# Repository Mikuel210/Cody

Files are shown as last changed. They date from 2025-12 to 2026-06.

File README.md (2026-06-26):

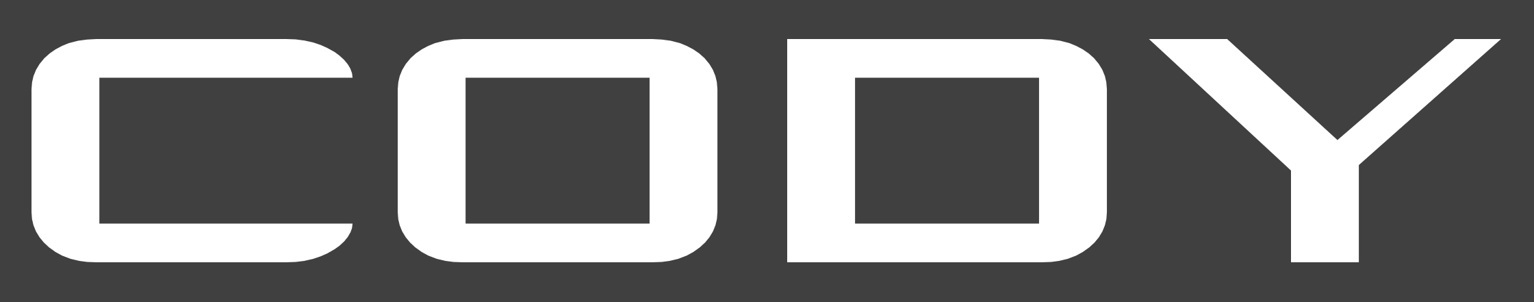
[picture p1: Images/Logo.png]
Cody


**Cody is a robot for the next season of WRO Robomission Senior.** 

The World Robot Olympiad (WRO) is a global robotics competition. For the Robomission challenge, you have to design, build and program a robot to complete a set of challenges on a board in under 2 minutes. Cody is our attempt at making our best robot so far, and I'm designing it to be faster, more precise and more reliable than all of our previous.

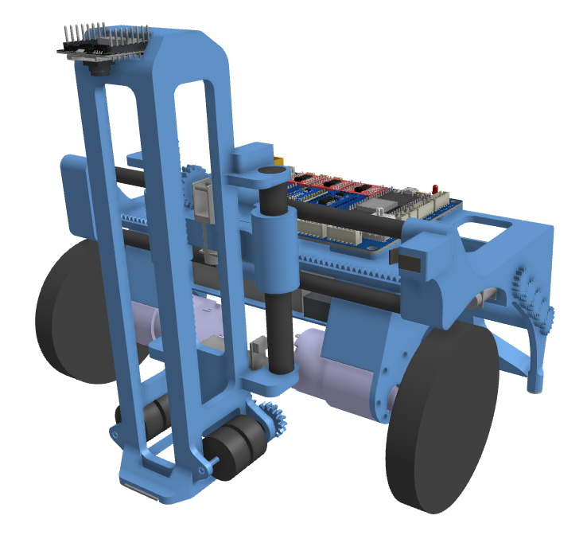
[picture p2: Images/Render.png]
Render


## This year's challenges

1. There is a mosaic with a randomized pattern of colors at the center of the board. You have to place a block of the right color in each square of the grid to score.

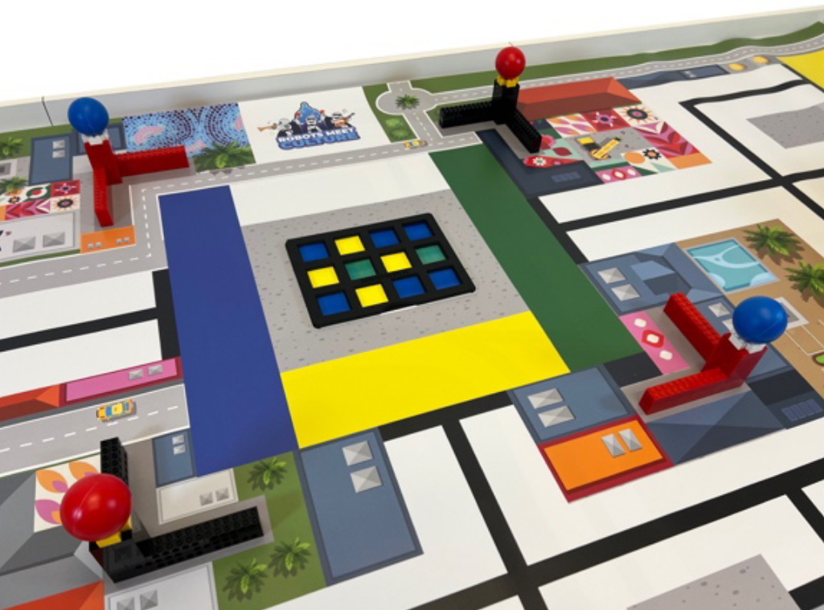
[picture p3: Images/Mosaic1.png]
Mosaic


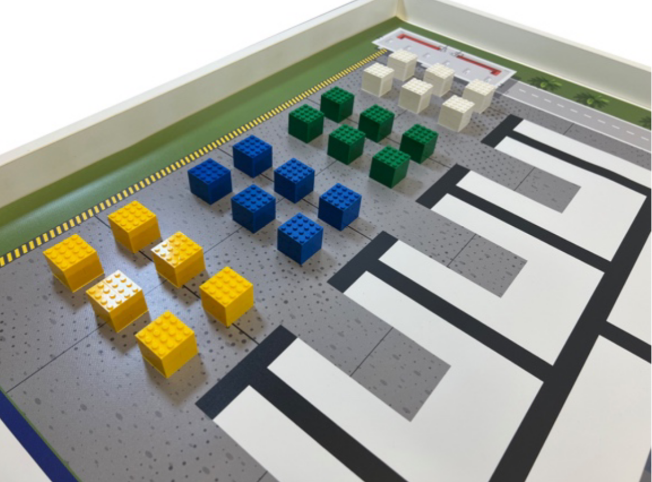
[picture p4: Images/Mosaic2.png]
Blocks


2. There are blocks of "cement" of different colors on the board. You have to carry the blocks of each color to their corresponding area.

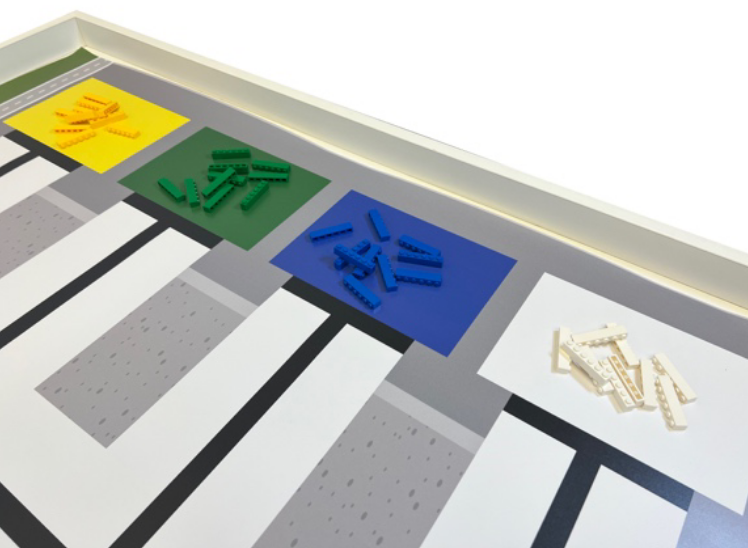
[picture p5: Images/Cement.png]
Cement


## Our solution

1. A toolhead grabs and drops blocks for the mosaic by using wheels

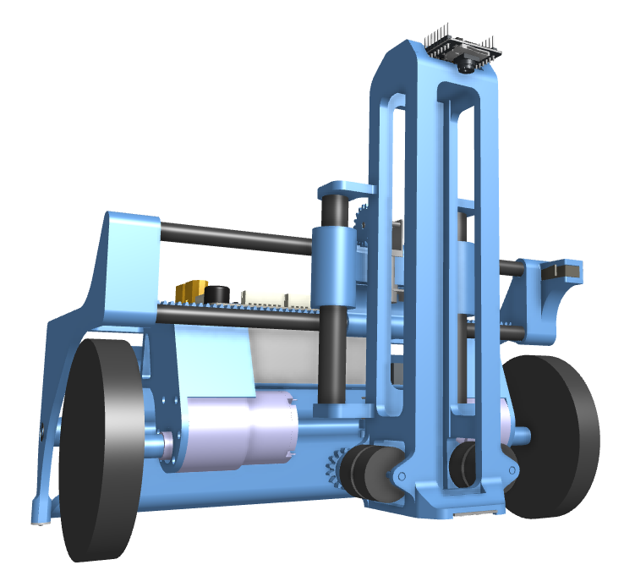
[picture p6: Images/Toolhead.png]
Toolhead


2. A mill picks up, carries and releases two colors of cement at a time

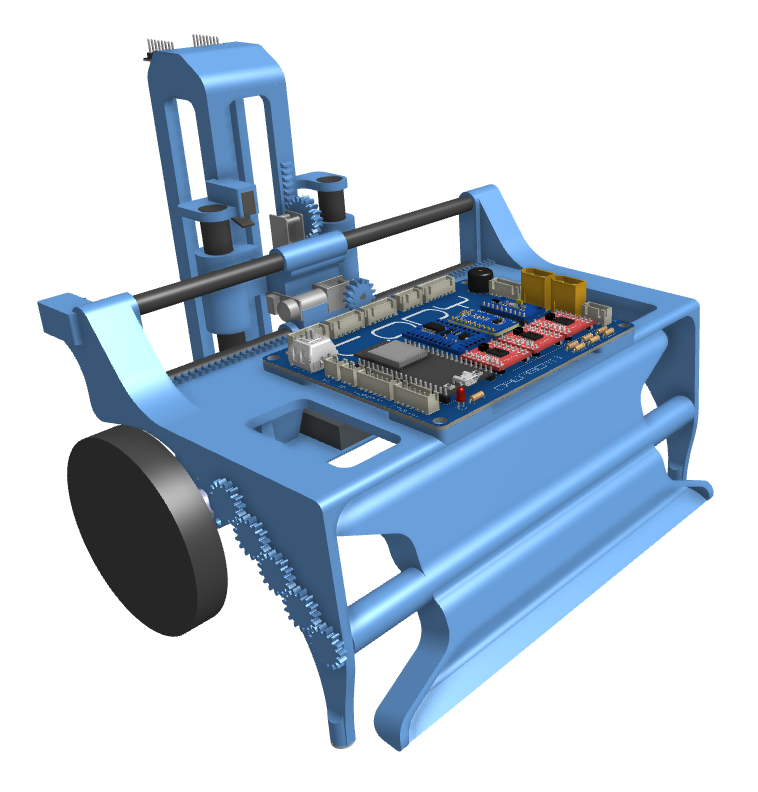
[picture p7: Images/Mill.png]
Mill


## How it works

- **Electronics:** I'm using an ESP32 as the microcontroller, an MPU9250 IMU for orientation and a TCS34725 color sensor for detecting the lines on the board. I'm also using an ADS1115 ADC for measuring the voltage of the battery and a PCF8575 GPIO expander.
- **Camera:** I'm using an ESP32-CAM to detect the color pattern of the mosaic.
- **Actuators:** I'm using JGB37-3530 motors for the wheels and N20 motors for the toolhead and for the mill. I'm using TB6612FNG drivers to control them.
- **Power:** I'm using a 3S 2200mAh LiPo battery for powering the robot. I'm also using a voltage regulator for powering the ESP32.
- **Structure:** I'm using 3D printed structural parts that have attachments for the components. I will be printing them out of PETG. I'm also using standard hardware such as bearings, carbon fiber rods and castor wheels.
- **Software:** I'm using odometry and a Pure Pursuit algorithm for control.

## Why I made this

My team has been using Lego Spike since we started competing, but it's starting to show its limitations. Last year, we went to the international final for the first time. Robomission had opened up to all hardwares for the first time this year, which means other teams could make faster, more precise and more reliable robots than what we could possibly do with Lego. I'm designing this robot to be faster, more precise and more reliable than our previous robots with the power of open hardware.

## PCB

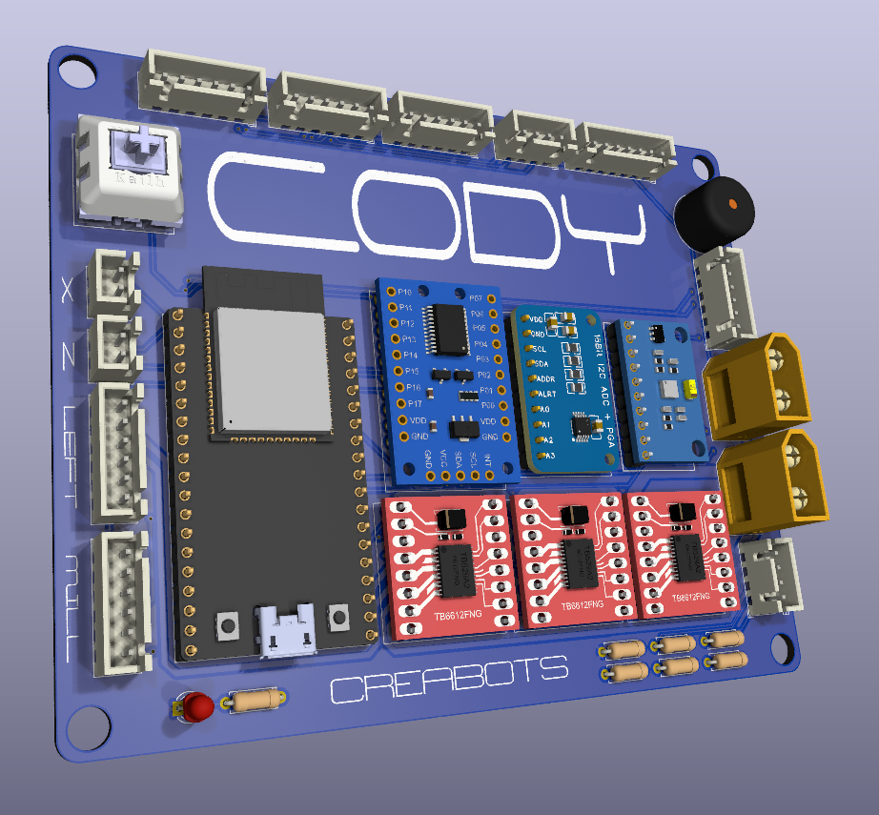
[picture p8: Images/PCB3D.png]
PCB 3D model


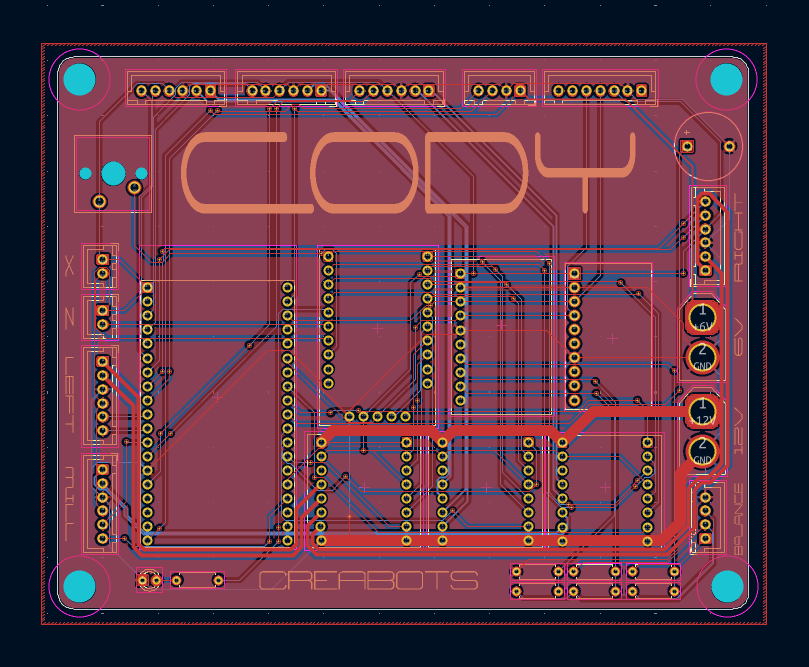
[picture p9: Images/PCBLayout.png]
PCB Layout


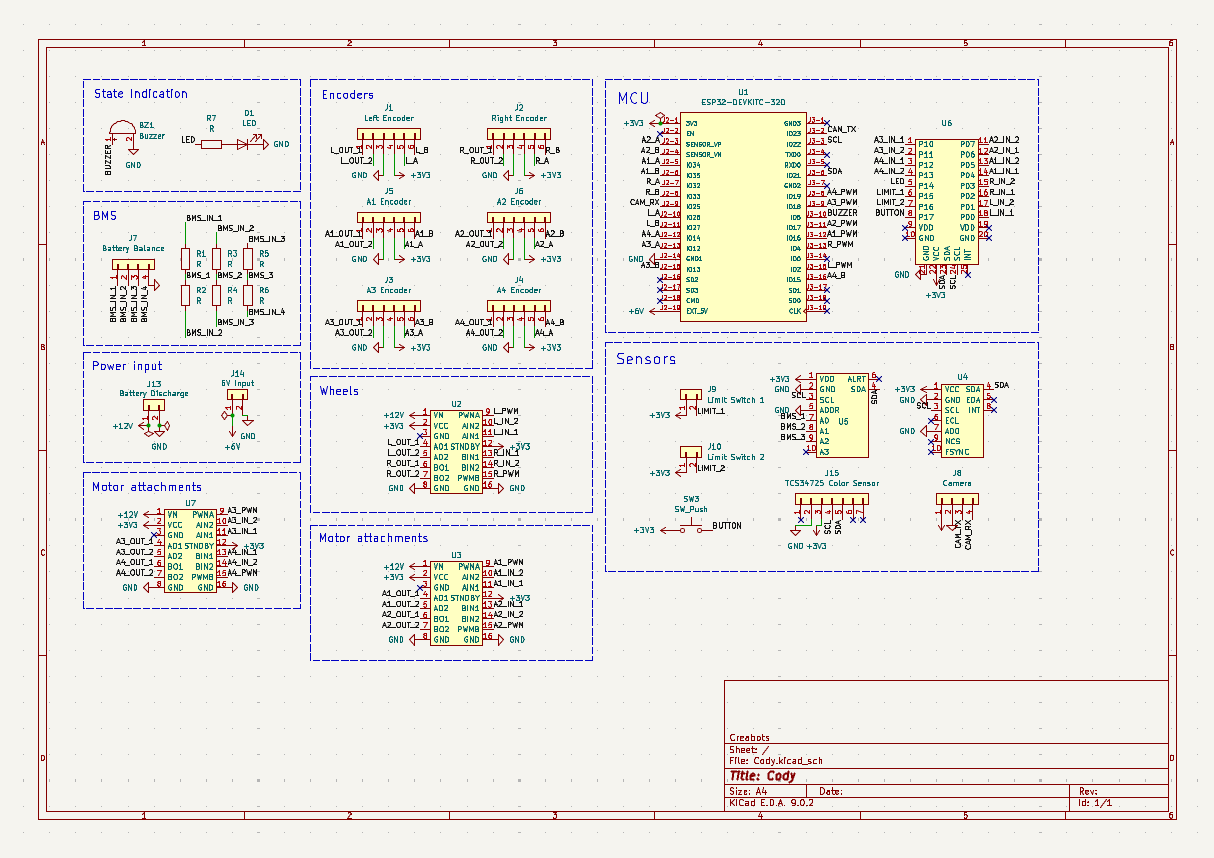
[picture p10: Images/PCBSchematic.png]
PCB Schematic


## Wiring diagram

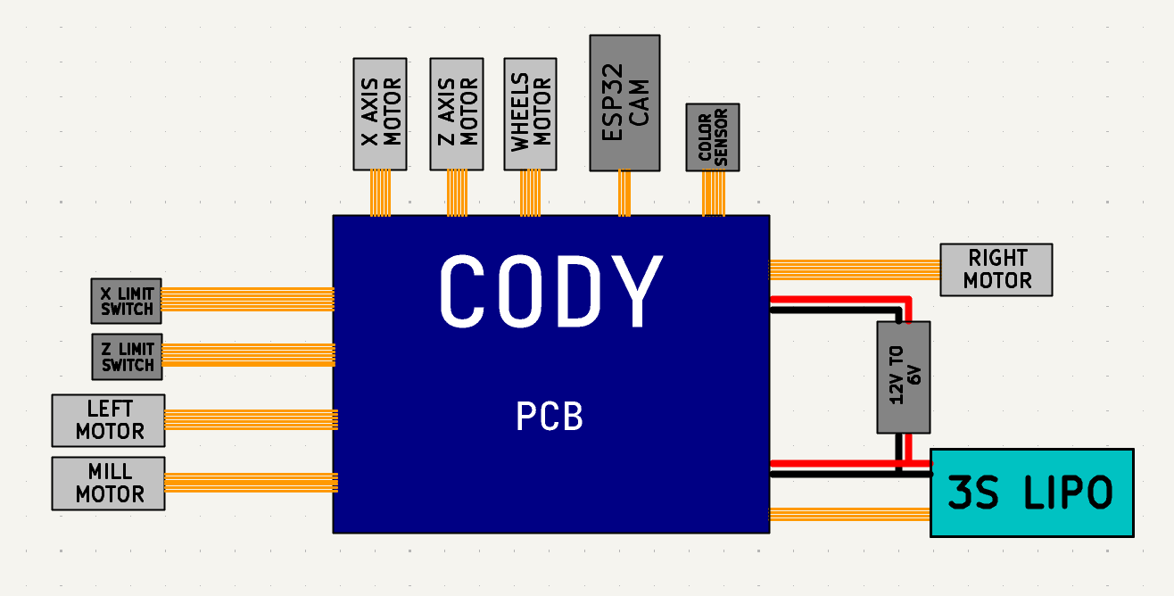
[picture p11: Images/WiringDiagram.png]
Wiring diagram


## Onshape Document

https://cad.onshape.com/documents/a1e1109ed4daddff079aebb8/w/75daa850bdae83d3a805f11b/e/0ab81b698f3d6ebcf8c57589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

## Cart screenshots

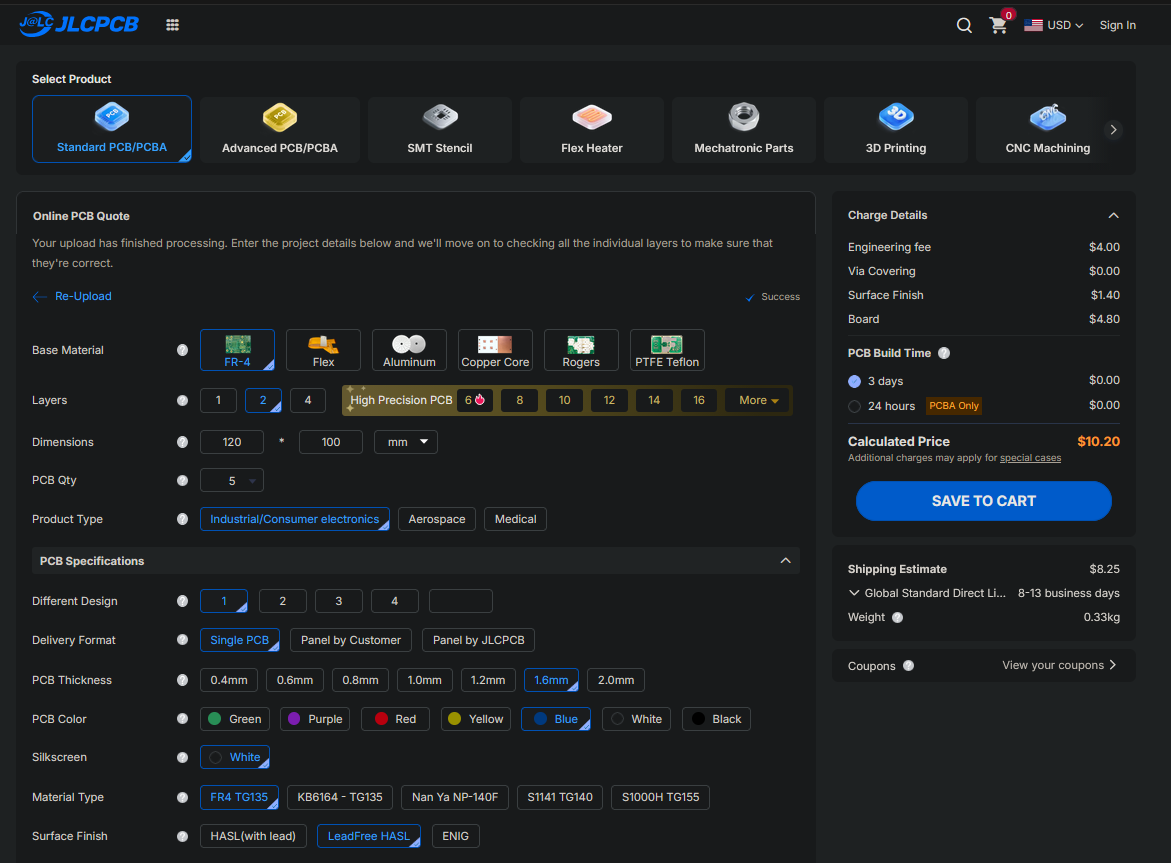
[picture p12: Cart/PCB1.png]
Cart screenshot

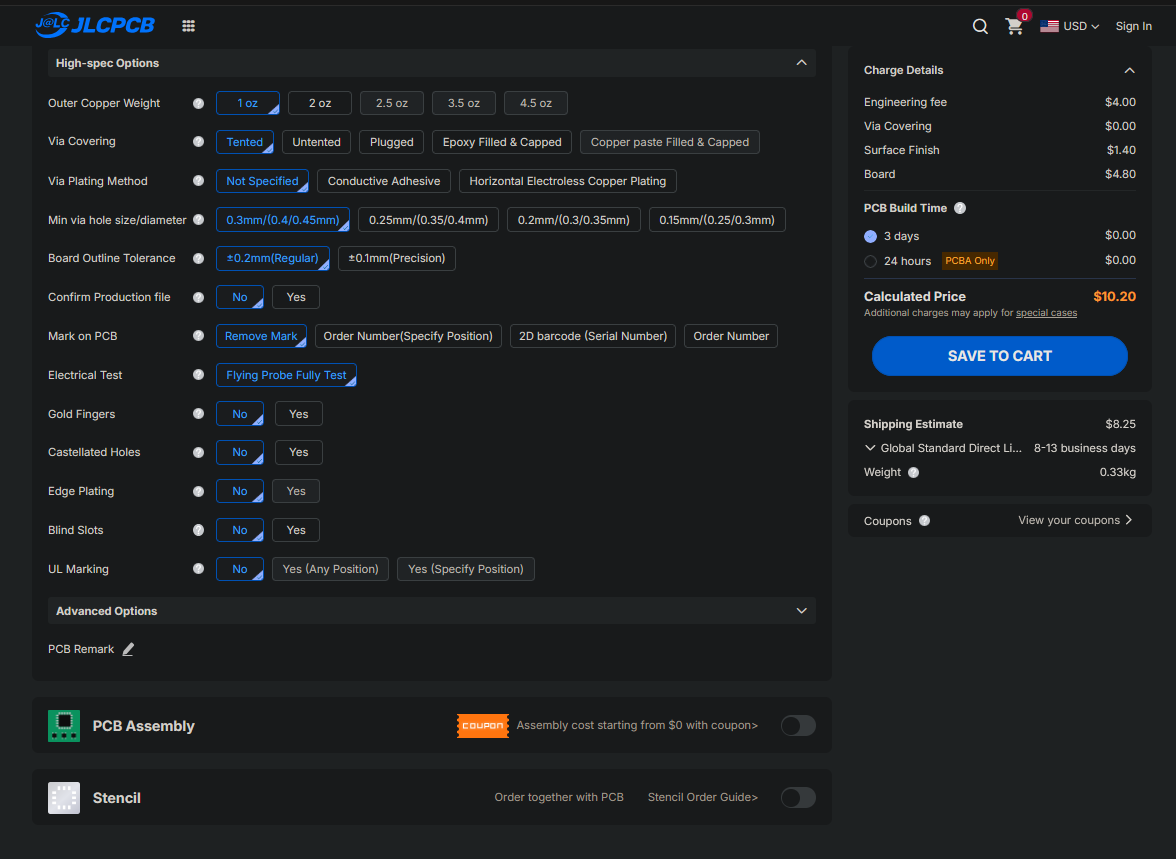
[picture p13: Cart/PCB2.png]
Cart screenshot

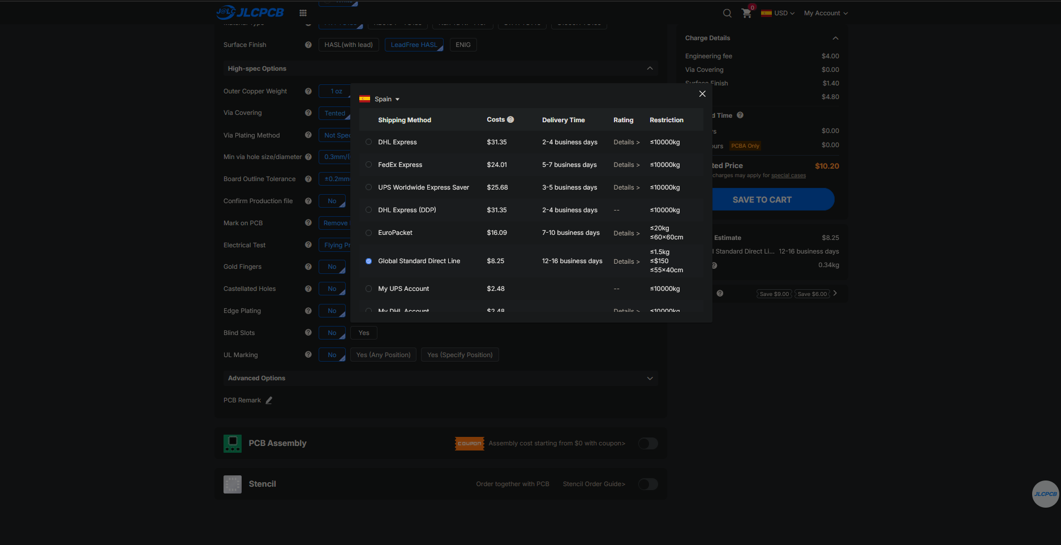
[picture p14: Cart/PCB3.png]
Cart screenshot

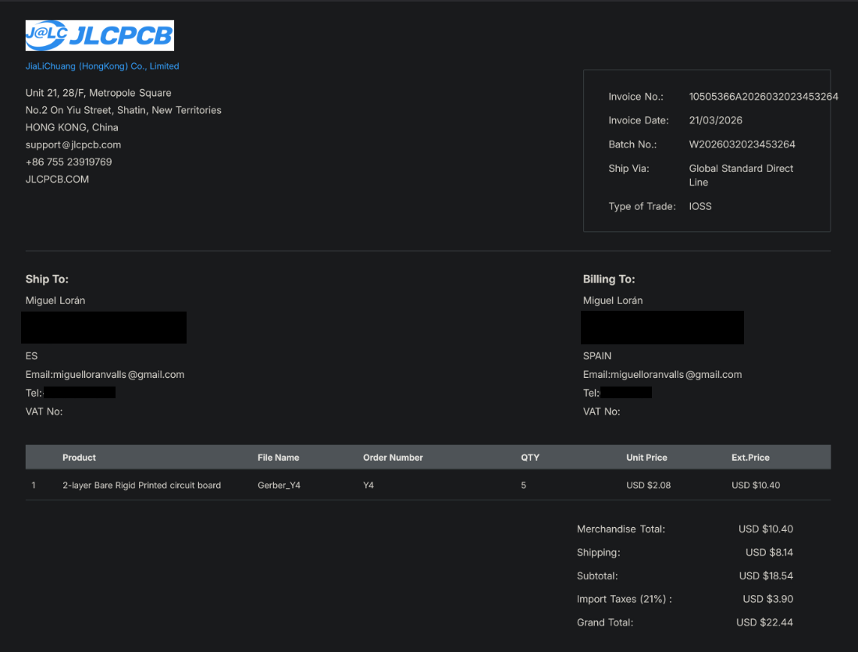
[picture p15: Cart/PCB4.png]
Cart screenshot

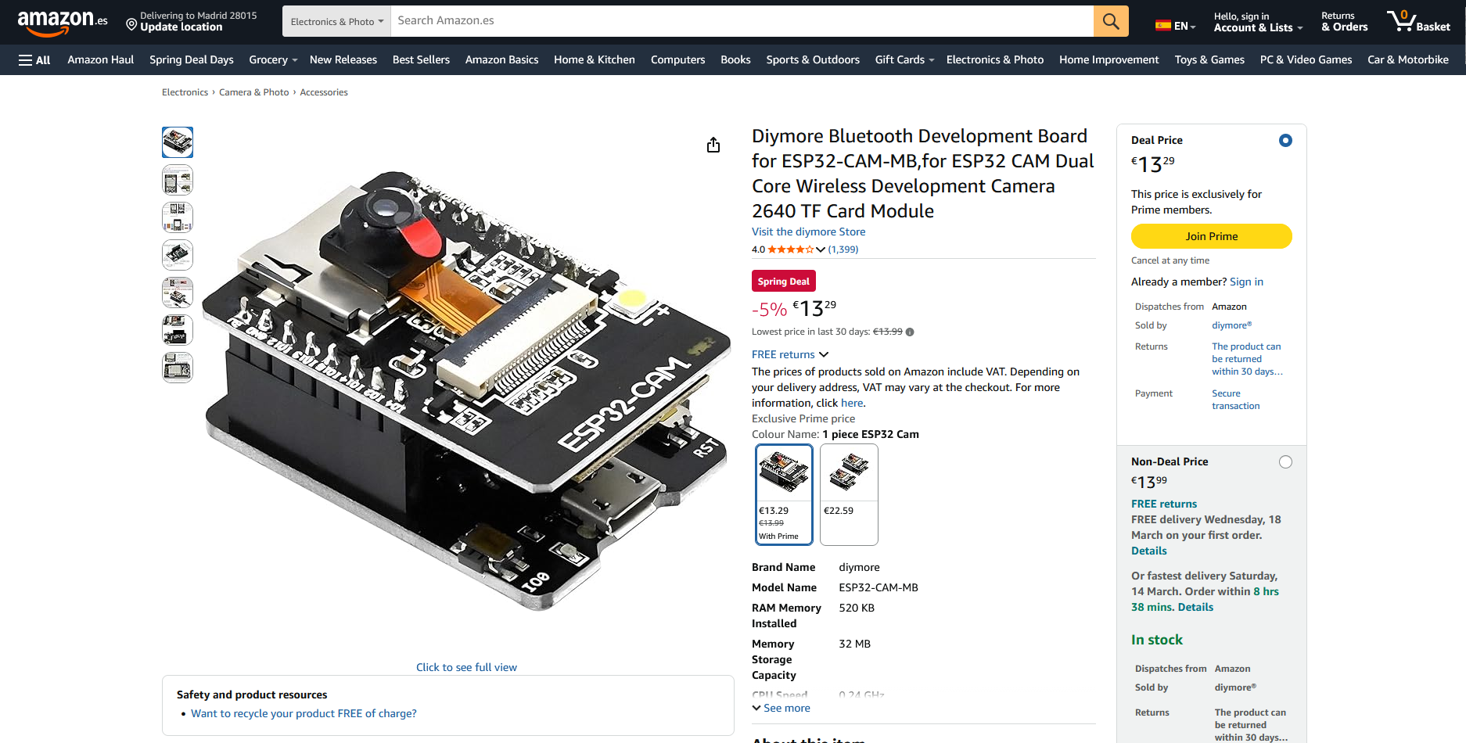
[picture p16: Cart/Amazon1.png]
Cart screenshot

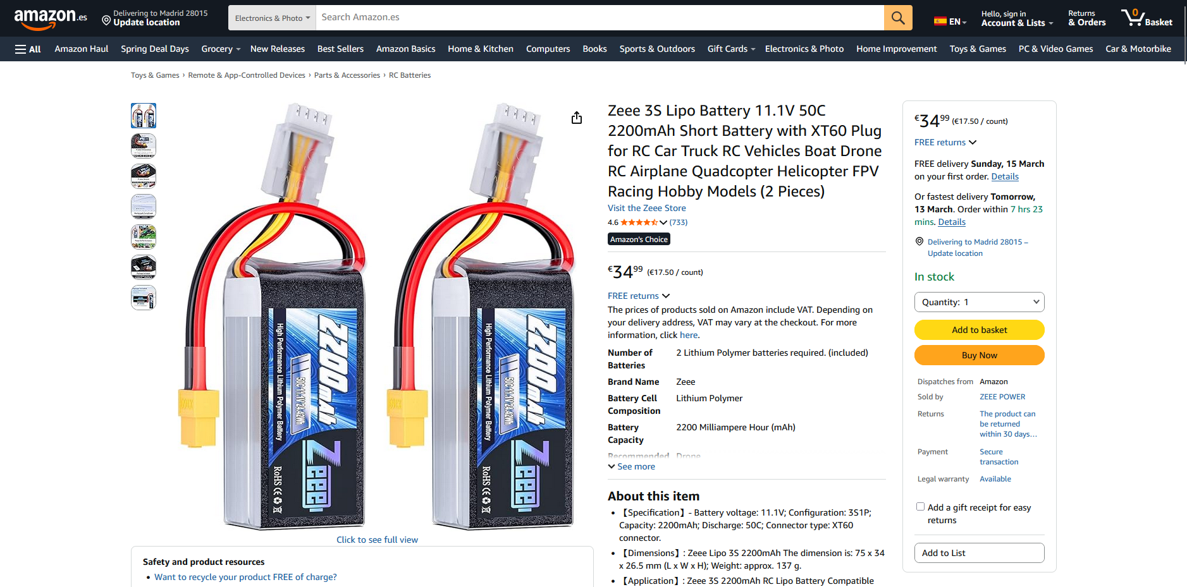
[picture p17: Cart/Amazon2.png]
Cart screenshot

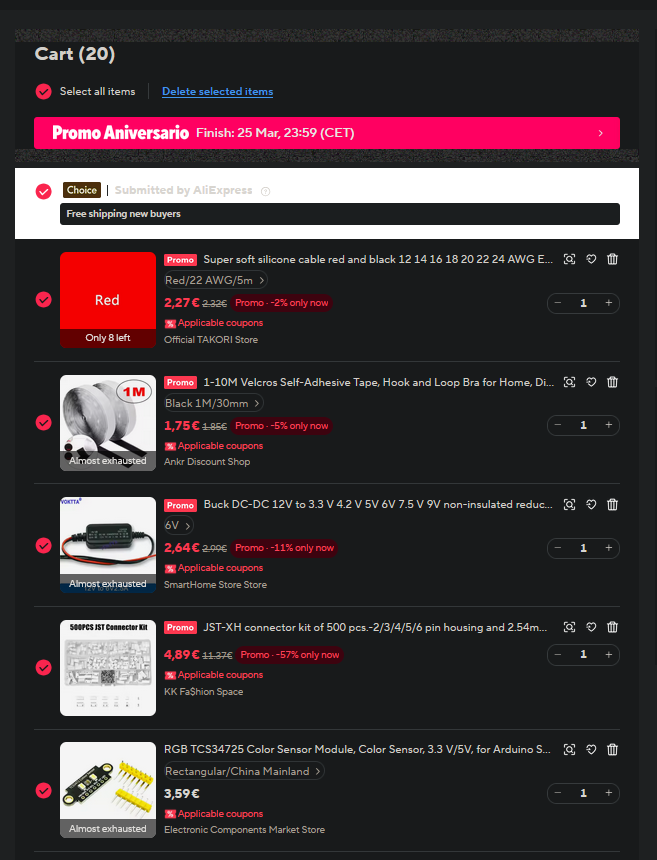
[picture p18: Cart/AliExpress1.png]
Cart screenshot

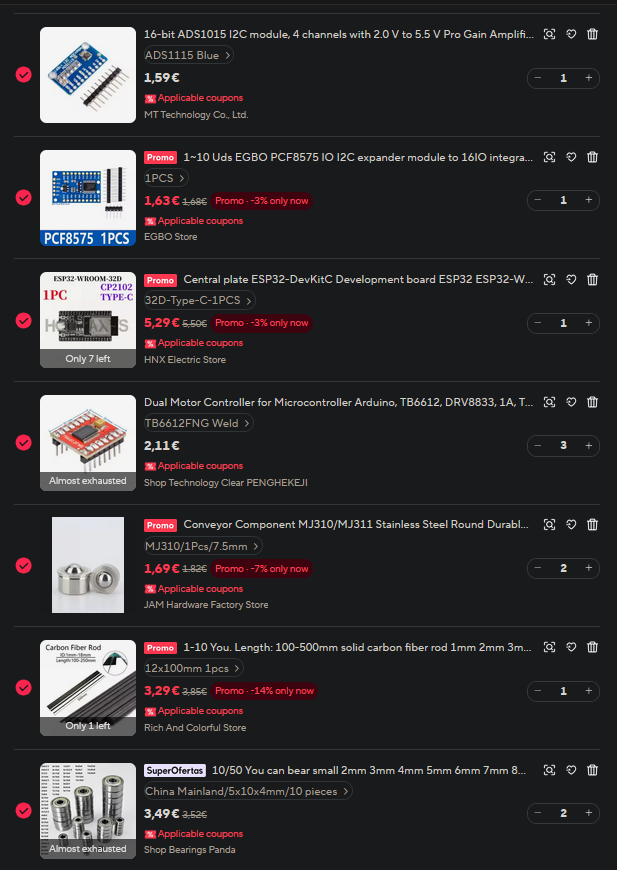
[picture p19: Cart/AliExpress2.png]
Cart screenshot


> Note: I will be buying two of the carbon fiber rods above but AliExpress didn't feel like allowing me to add more than one to my cart at the moment

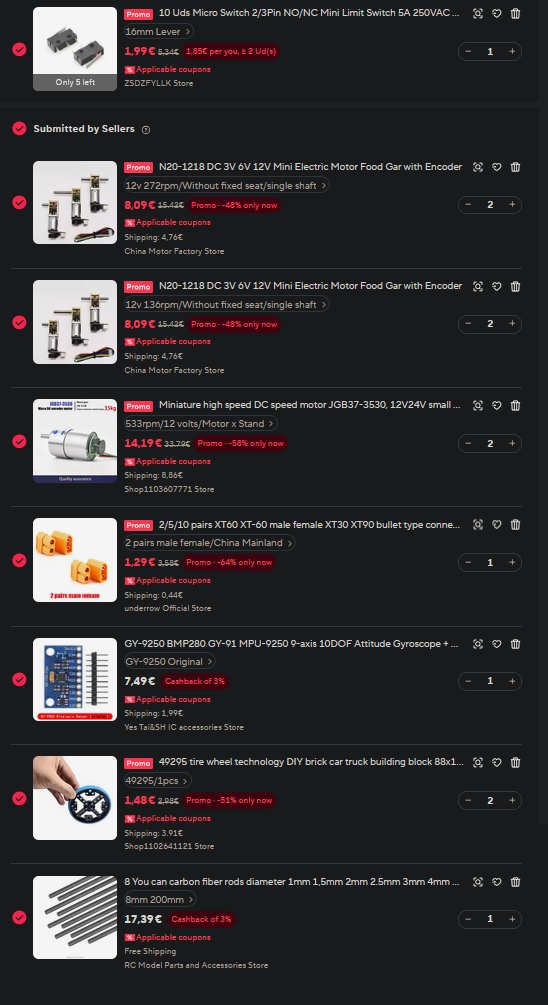
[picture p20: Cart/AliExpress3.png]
Cart screenshot

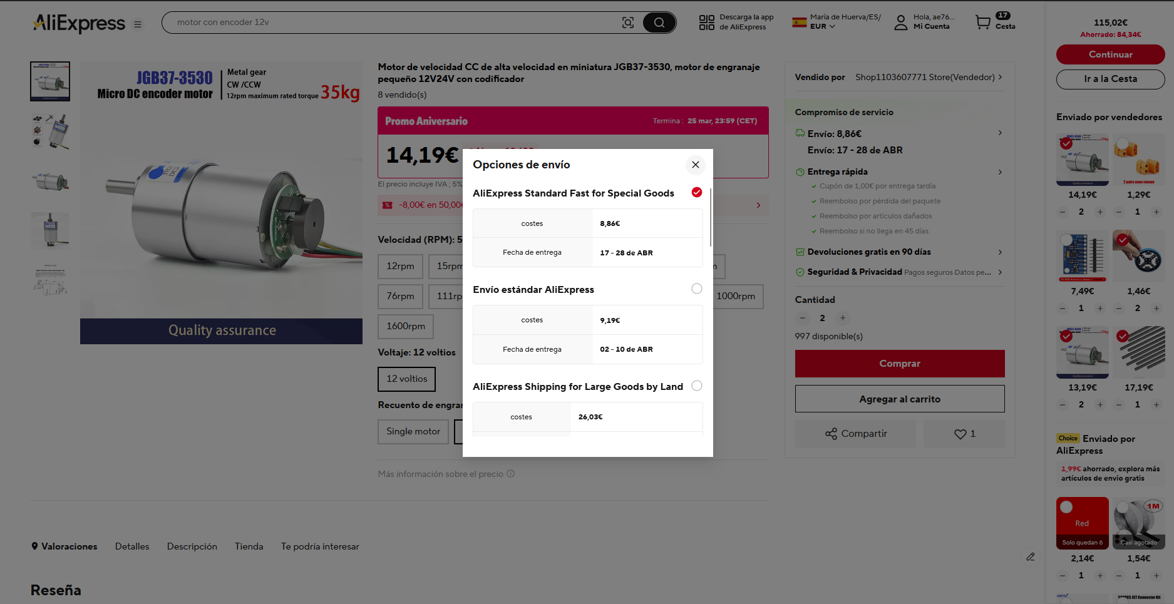
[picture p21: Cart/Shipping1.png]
Cart screenshot

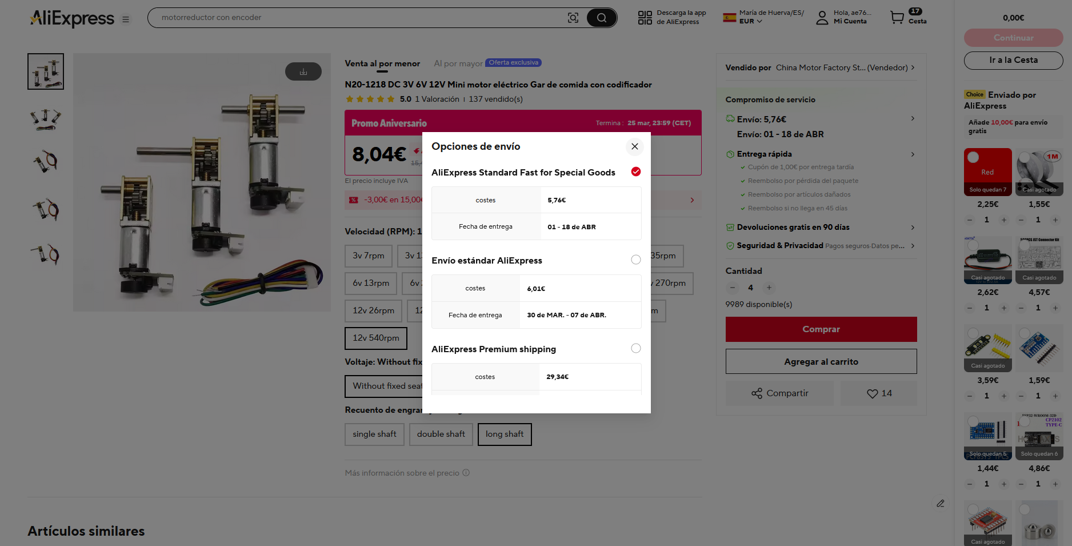
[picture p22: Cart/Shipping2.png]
Cart screenshot

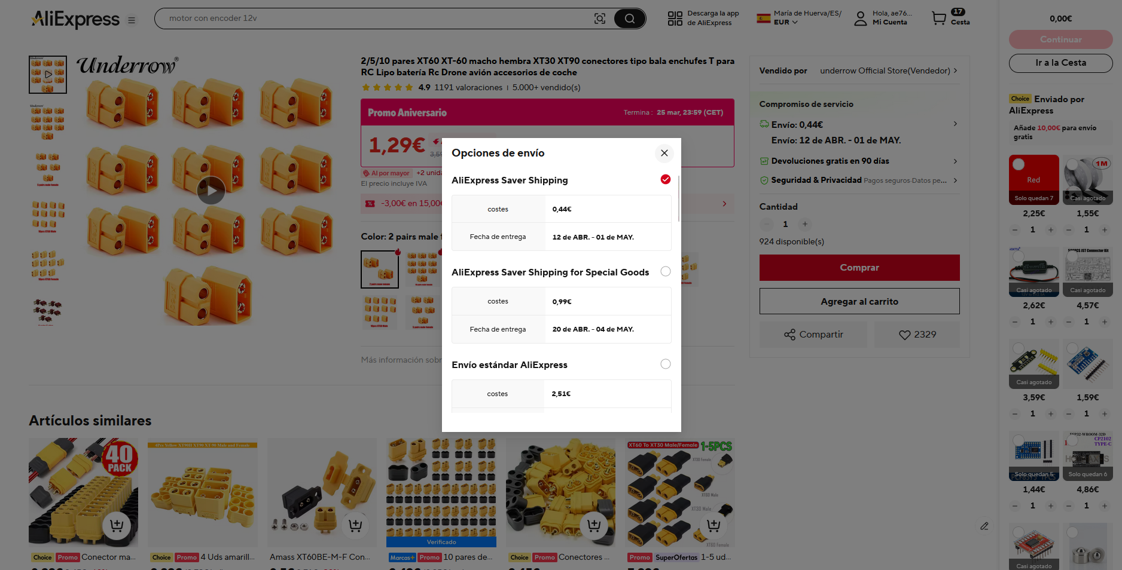
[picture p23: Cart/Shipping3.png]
Cart screenshot

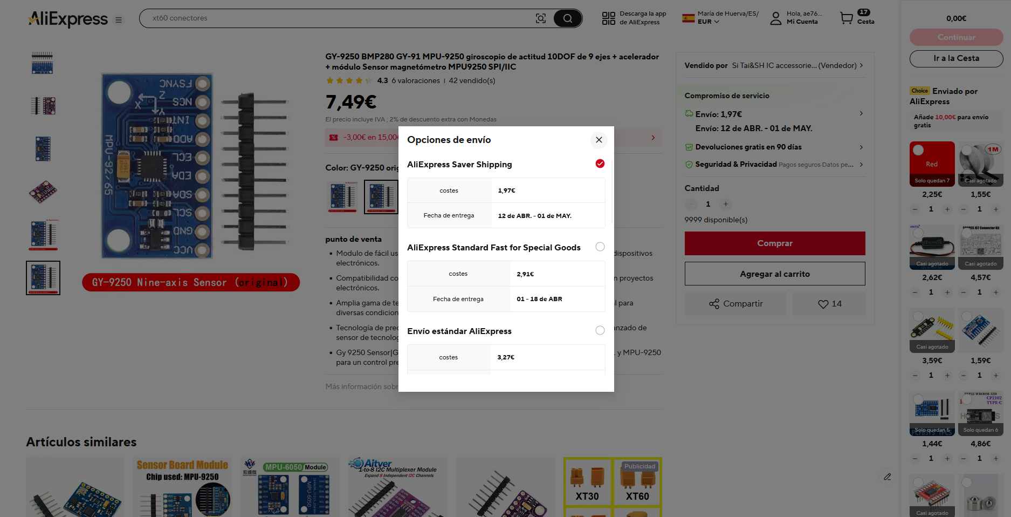
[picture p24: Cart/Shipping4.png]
Cart screenshot

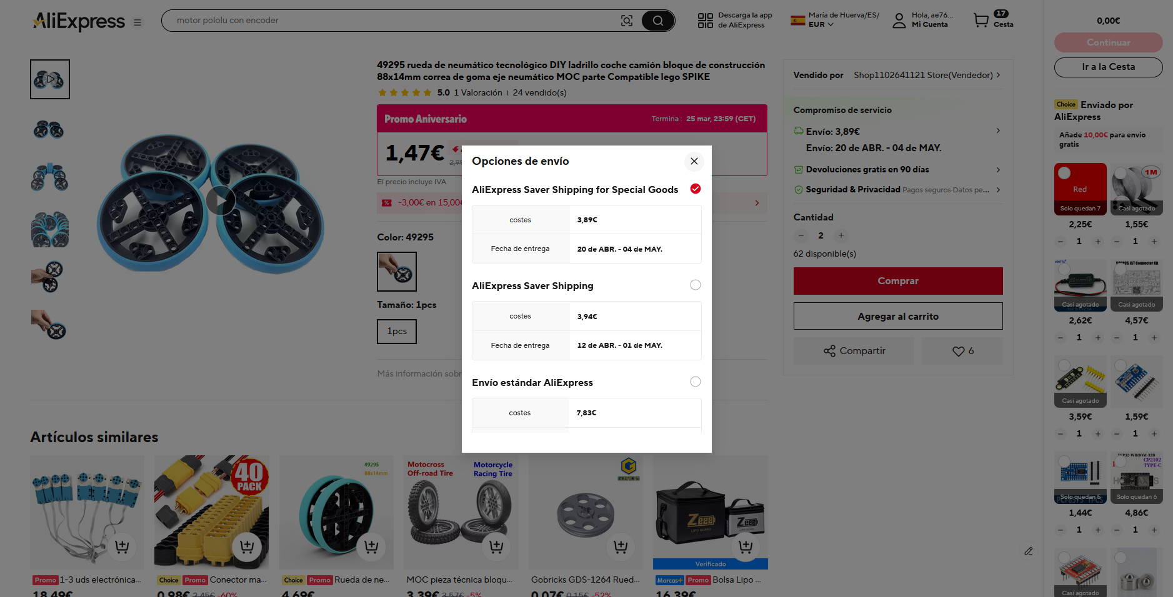
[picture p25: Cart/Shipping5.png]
Cart screenshot


## BOM

> Note that the amount to buy might be higher than the amount to be used because the item is sold in bulk

|Item |Amount|Amount to buy|Unit price|Total price |Link |Config |
|---|---|---|---|---|---|---|
|PETG |1 |0 |0,00 € |0,00 € |- |- |
|PCB |1 |1 |19,36 € |19,36 € |https://jlcpcb.com |- |
|Battery |2 |2 |17,50 € |34,99 € |https://www.amazon.es/Zeee-Bater%C3%ADa-Veh%C3%ADculos-Cuadric%C3%B3ptero-Helic%C3%B3ptero/dp/B0BYNSH6Q7|- |
|X Axis rods |2 |8 |2,17 € |17,39 € |https://es.aliexpress.com/item/4001063505625.html |8mm 200mm |
|Z Axis rods |2 |2 |3,29 € |6,58 € |https://es.aliexpress.com/item/1005006793821681.html |12x100mm 1pcs |
|Wheel motors |2 |2 |18,62 € |37,24 € |https://es.aliexpress.com/item/1005008730235398.html |533rpm 12V Motor x Stand |
|N20 motors |4 |4 |10,47 € |41,88 € |https://es.aliexpress.com/item/1005009284080839.html |136x2, 272x2 without fixed seat|
|Front wheels |2 |2 |3,44 € |6,87 € |https://es.aliexpress.com/item/1005010058308140.html |49295 1pcs |
|Back wheels |2 |2 |1,69 € |3,38 € |https://es.aliexpress.com/item/1005005334424631.html |7.5mm 1Pcs MJ310 |
|5x10x4 Bearing |11 |20 |0,35 € |6,98 € |https://es.aliexpress.com/item/1005007668446060.html |5x10x4mm |
|Buzzer |1 |0 |0,00 € |0,00 € |- |- |
|RGB LED |1 |0 |0,00 € |0,00 € |- |- |
|Resistors |7 |0 |0,00 € |0,00 € |- |- |
|Mechanical switch |1 |0 |0,00 € |0,00 € |- |- |
|Limit switches |2 |10 |0,20 € |1,99 € |https://es.aliexpress.com/item/1005008823539259.html |16mm Lever |
|TB6612FNG Motor drivers |3 |3 |2,11 € |6,33 € |https://es.aliexpress.com/item/1005006983040834.html |TB6612FNG Weld |
|ESP32 DevKitC |1 |1 |5,29 € |5,29 € |https://es.aliexpress.com/item/1005008256121637.html |32D-Type-C-1PCS |
|PCF8575 GPIO Expander |1 |1 |1,63 € |1,63 € |https://es.aliexpress.com/item/1005002073772322.html |1PCS |
|ADS1115 ADC |1 |1 |1,59 € |1,59 € |https://es.aliexpress.com/item/32311656694.html |ADS1115 Blue |
|MPU9250 IMU |1 |1 |9,48 € |9,48 € |https://es.aliexpress.com/item/1005009033822037.html |GY-9250 original |
|TCS34725 Color sensor |1 |1 |3,59 € |3,59 € |https://es.aliexpress.com/item/1005006292597348.html |Rectangular |
|XT60 Connectors |2 |2 |0,87 € |1,73 € |https://es.aliexpress.com/item/1005004628891959.html |2 pairs male female |
|JST-XH Connectors |9 |9 |0,54 € |4,89 € |https://es.aliexpress.com/item/1005008638438956.html |- |
|12V to 6V converter |1 |1 |2,64 € |2,64 € |https://es.aliexpress.com/item/1005007763337343.html |6V |
|ESP32-CAM |1 |1 |13,29 € |13,29 € |https://www.amazon.es/diymore-desarrollo-ESP32-CAM-MB-Bluetooth-inal%C3%A1mbrica/dp/B08X3GRK22 |- |
|Velcro for battery and converter|1 |1 |1,75 € |1,75 € |https://es.aliexpress.com/item/1005008938790125.html |Black 1M 30mm |
|Cable for sensors and motors |1 |1 |2,27 € |2,27 € |https://es.aliexpress.com/item/1005006566120439.html |5m 22 AWG |
|Cable for battery |1 |0 |0,00 € |0,00 € |- |- |
|TOTAL | | | |231,14 € ($267,79)| | |

---

Made with ❤️ for Blueprint thanks to Hack Club

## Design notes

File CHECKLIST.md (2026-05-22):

- [x] Finish BOM
- [x] Finish firmware
- [-] New renders
- [x] Update GitHub
- [x] Submit to Blueprint
- [x] Buy parts
- [x] Update CAD model
	- [x] New motors (N20 / N30)
	- [x] Limit switches
	- [x] Camera and color sensor
	- [x] Switch to CF rods
- [x] Check amperages and weight
- [x] Update PCB (01-04-2026)
	- [x] Add button
	- [x] Limit switch connectors
	- [x] Camera connector requires power pins
	- [x] Connector placement collides with X axis
	- [x] Make sure amperages work out
	- [x] Check I2C addresses
	- [x] Better routing
	- [x] Proper silkscreen for connectors
- [x] Update Blueprint journal and repo
- [x] Calculate cable length
- [x] Buy remaining parts (01-04-2026)
- [x] Update measurements (01-04-2026)
	- [x] New motor mounts
- [x] Prototyping
	- [x] Motor mounts
		- [x] N20
		- [x] Wheels
	- [x] CF rod attachments and sliding
		- [x] .15 -> A tiny bit loose for sliding
		- [x] .14 -> Still a bit loose
		- [x] .13 -> Sweet spot
		- [x] .12 -> Sweet spot
	- [x] X Axis attachments
	- [x] Bearings
	- [x] Limit switches
	- [x] N20 attachments
	- [x] ESP32-CAM
	- [x] Color sensor
	- [x] Castor wheels
- [/] Get reimbursed
- [/] Building and assembly (01-05-2026)
	- [x] Print tube (19-04-2026)
		- [x] Print new gears
		- [x] Glue wheels
	- [x] Print chassis
		- [x] Prepare for printing
		- [x] Consider buying new wheels
	- [x] Print gears
	- [x] Print bolts
	- [x] Print wheel adapters
	- [ ] Print new mill
		- [x] Test plastic thingy
- [/] Coding (06-06-2026)
	- [x] Pure Pursuit
	- [x] Move toolhead
	- [x] Toolhead paths
	- [x] Moving wheels
	- [x] Moving mill
	- [>] Camera
	- [x] Color sensor
	- [x] Color fusion
	- [x] BMS
		- [x] Read voltage
		- [x] Smooth in fusion
		- [x] Alarm if too low
	- [x] State indication
	- [x] Limit switches
	- [x] Button
	- [x] Homing
	- [ ] Home mill
	- [ ] Camera integration
	- [ ] Align with wall
	- [ ] Stop in line
	- [ ] Block picking algorithm
- [/] Testing in simulation
	- [x] Button
	- [x] BMS
	- [x] Movement
	- [x] Toolhead
	- [x] Homing
	- [ ] Wheels
	- [ ] Mill
	- [ ] Color sensor
	- [ ] Camera
- [/] Cut cables
	- [x] X
	- [x] Z
	- [x] Wheels
	- [ ] Camera
	- [ ] Color
	- [x] Mill
	- [ ] Balance
	- [x] Battery and voltage converter
- [/] Solder/crimp connectors
- [/] Integrated testing (04-07-2026)
	- [/] Get BMS to work
	- [ ] Get Cody.h to work

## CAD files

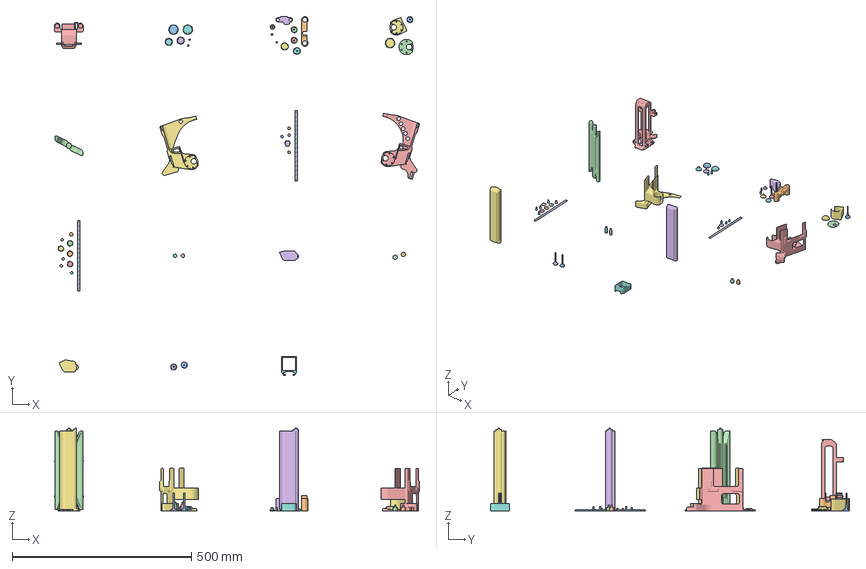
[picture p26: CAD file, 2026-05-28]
Slicer/Main.3mf
1019.0 x 1001.1 x 230.8 mm
Main - Chassis.step x 2
Part Studio 1 - Left wheel adapter.step x 2
Spur gear (15 teeth) x 5
Left wheel adapter
Chassis x 2
Right wheel adapter
Toolhead - Spur gear (15 teeth).step
X Axis right limit x 3
Main - Mill.step x 2
Spur gear (26 teeth) x 3
Landing leg bolt - Bolt.step x 4
Wheel attachment - Left wheel adapter.step
Landing leg bolt Copy 1 - Bolt.step x 4
Wheel attachment - Chassis.step x 2
Toolhead - Tube.step
Spur gear (18 teeth) x 3
X Axis carriage x 2
Toolhead - Spur gear (18 teeth).step
Spur gear (12 teeth)
Main - Mill(6).step
Main - Mill(2).step
Part Studio 2 - Part 2.step

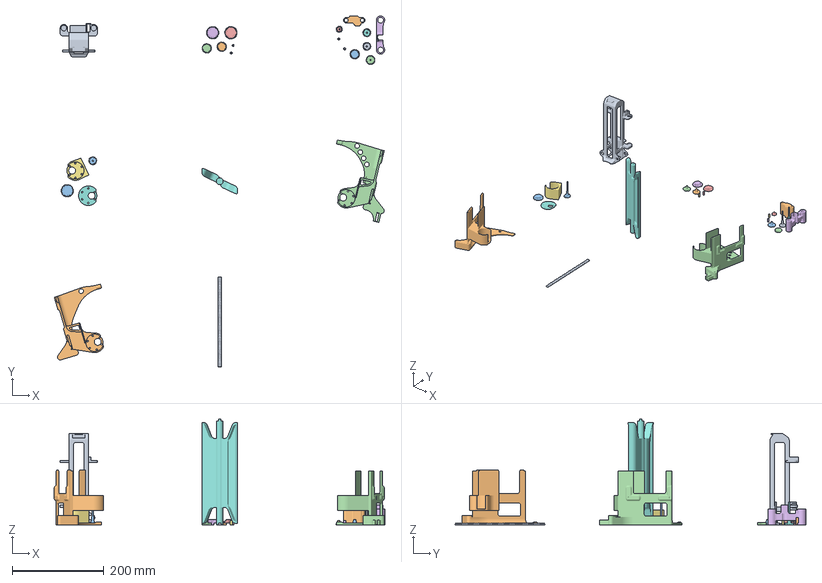
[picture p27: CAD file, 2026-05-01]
Slicer/Main.sync-conflict-20260428-161026-ZBDHWGP.3mf
720.9 x 765.4 x 230.8 mm
Chassis x 3
Toolhead - Spur gear (15 teeth).step
Spur gear (26 teeth) x 3
Wheel attachment - Chassis.step x 2
Toolhead - Tube.step
Spur gear (18 teeth) x 3
X Axis carriage x 2
Spur gear (15 teeth) x 2
Toolhead - Spur gear (18 teeth).step
Spur gear (12 teeth)
Main - Mill.step

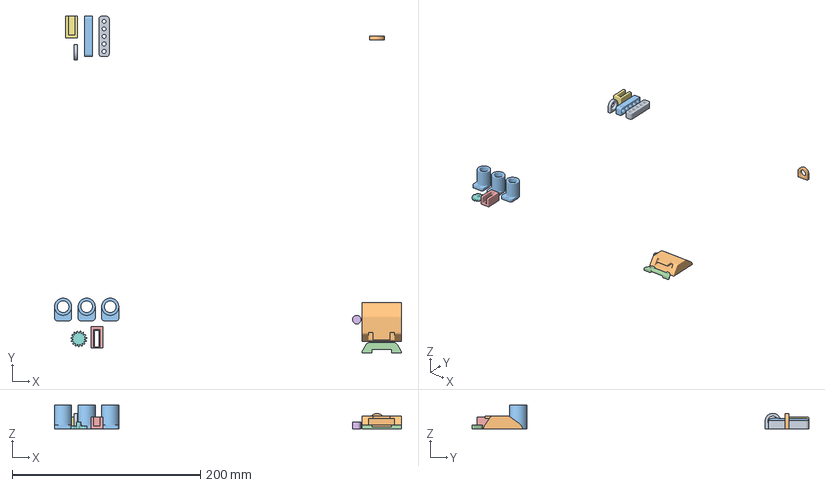
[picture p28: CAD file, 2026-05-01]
Slicer/Prototypes.3mf
368.2 x 357.2 x 25.0 mm
ESP32-CAM - Tube.step
Color sensor - Tube.step
Limit switch attachment - Chassis.step x 2
Castor wheel - Chassis.step
Main - X Axis right limit.step
Bearing attachment - Part 1.step
Bearing attachment - Part 1(1).step
Z Axis tolerance 2.step

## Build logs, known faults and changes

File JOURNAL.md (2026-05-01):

uhhhhhh check hacka???

## today, 27-03::::

16 20 to 19 00

I've made the simulation, managed to connect it to the esp, set up command and data system and created new simulationproviders, then tried to make it go to a point but uh not really

## 28-03

10 00 to 12 10 ish

13 20 to 22ish

ive added pure pursuit!!!!!!!!!!!!!!!! and it actually works pretty well
 
-lunch and walk so:::
-2h 30 or more

## 29-03

11 30 to 14 50

ive fixed spinning and finetuned pure pursuit, then i tested it on the board and broek apart, spent most of the time fixing it but the spinning is back :nooooovanish:

## 30-03

11 05 to 11 15?

15 55 to 12 05

15 05 to 15 20

im adding toolhead control!!!!!! !!!
but it kinda doesnt work

16 15 to 19 10

## 01-04

12 30 to 55

## 02-04

2h 30

I've been refactoring. Now pursuit is only pursuit lol and ive been implementing it for toolhead as well. im having issues with the sim and loading code so im not testing it for now. im also abstracting away goto and path code so that it can be used for the toolhead as well. and now the api is not the same as pursuit (new Cody class).

## 10-04

hey bro so check windows bc i have more entries there

15 50 ish to 18 00 or a bit more

so ive changed the cad to use the new n20 mounts!! and ive updated basically all measurements

# 11 04

1h 30min ish, ive printed prototypes (gear, cf rod, limit switch) and changhed the cad to use the new n20 mounts for the mill.

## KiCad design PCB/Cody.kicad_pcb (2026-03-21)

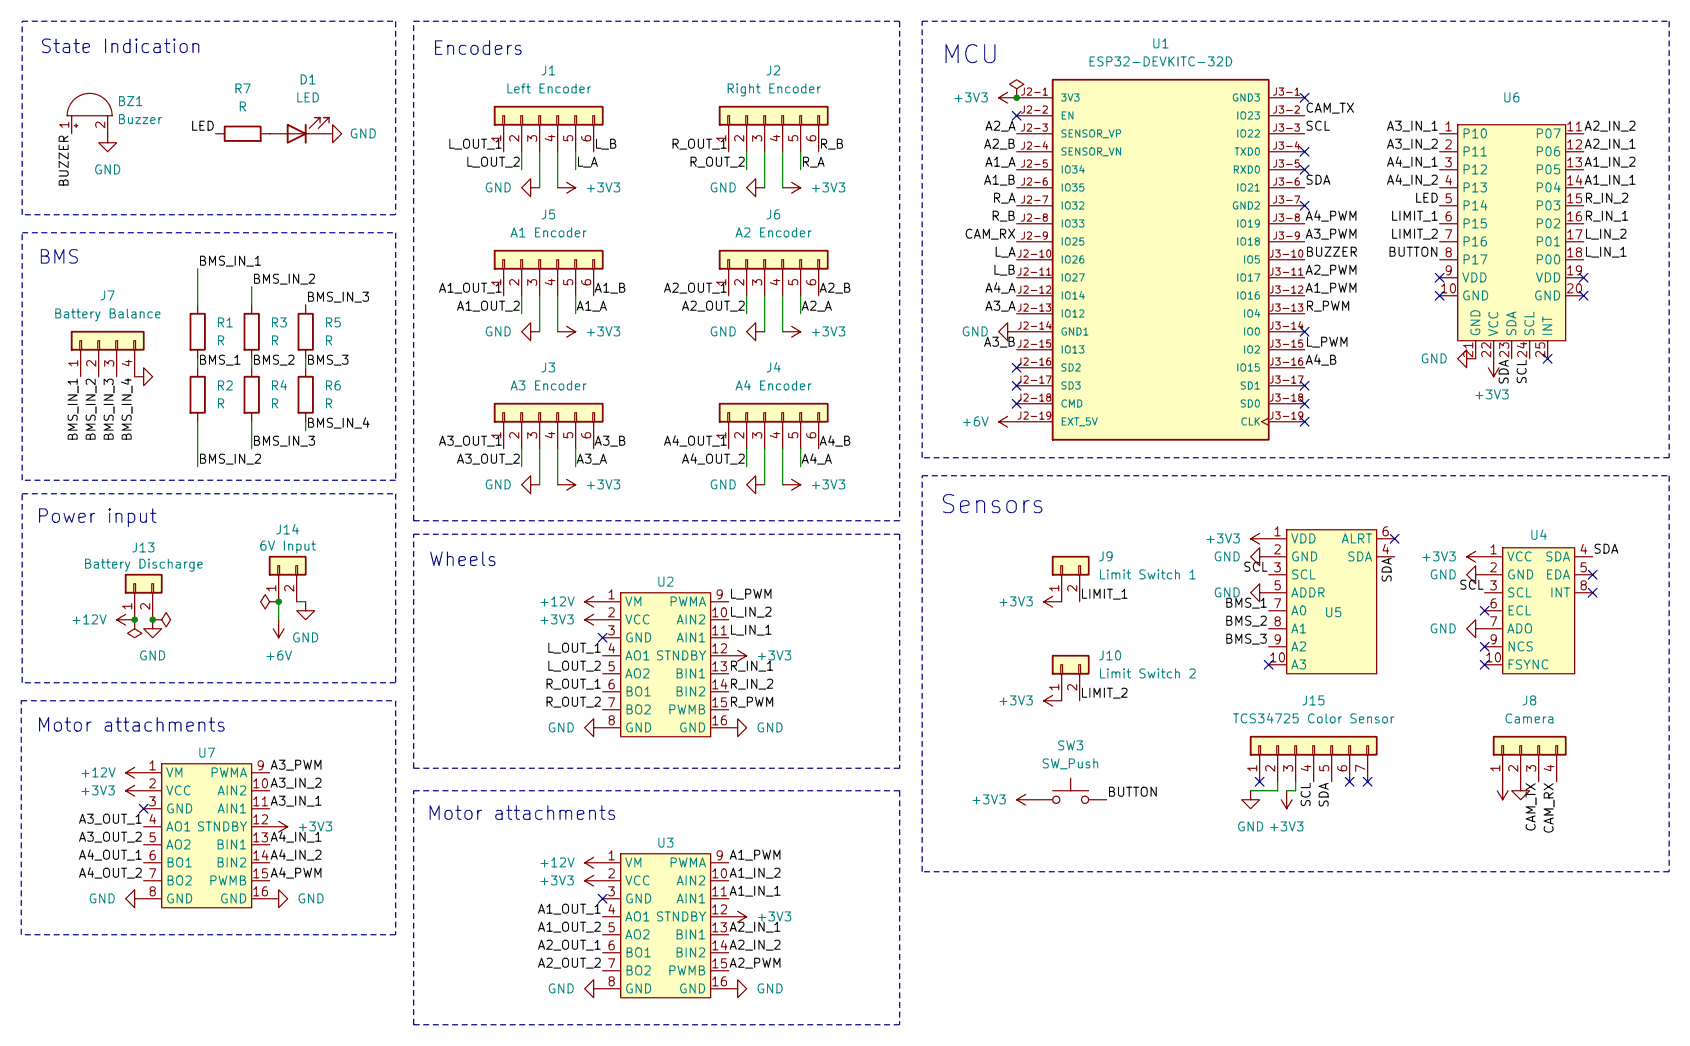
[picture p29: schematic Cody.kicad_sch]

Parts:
BZ1: Buzzer; Buzzer_12x9.5RM7.6
D1: LED; LED_D3.0mm
J1: Left Encoder; JST_XH_B6B-XH-A_1x06_P2.50mm_Vertical
J2: Right Encoder; JST_XH_B6B-XH-A_1x06_P2.50mm_Vertical
J3: A3 Encoder; JST_XH_B6B-XH-A_1x06_P2.50mm_Vertical
J4: A4 Encoder; JST_XH_B6B-XH-A_1x06_P2.50mm_Vertical
J5: A1 Encoder; JST_XH_B6B-XH-A_1x06_P2.50mm_Vertical
J6: A2 Encoder; JST_XH_B6B-XH-A_1x06_P2.50mm_Vertical
J7: Battery Balance; JST_XH_B4B-XH-A_1x04_P2.50mm_Vertical
J8: Camera; JST_XH_B4B-XH-A_1x04_P2.50mm_Vertical
J9: Limit Switch 1; JST_XH_B2B-XH-A_1x02_P2.50mm_Vertical
J10: Limit Switch 2; JST_XH_B2B-XH-A_1x02_P2.50mm_Vertical
J13: Battery Discharge; AMASS_XT60-M_1x02_P7.20mm_Vertical
J14: 6V Input; AMASS_XT60-M_1x02_P7.20mm_Vertical
J15: TCS34725 Color Sensor; JST_XH_B7B-XH-A_1x07_P2.50mm_Vertical
R1, R2, R3, R4, R5, R6, R7: R; R_Axial_DIN0207_L6.3mm_D2.5mm_P7.62mm_Horizontal
SW3: SW_Push; SW_Cherry_MX_1.00u_PCB
U1: ESP32-DEVKITC-32D; PARTREV V4; DigiKey_Part_Number 1965-1000-ND
U2, U3, U7: TB6612FNG
U4: GY-9250
U5: ADS1115
U6: PCF8575

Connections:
+3V3: J1.4, J2.4, J3.4, J4.4, J5.4, J6.4, J9.1, J10.1, J15.3, SW3.1, U1.J2-1 (3V3), U2.2 (VCC), U2.12 (STNDBY), U3.2 (VCC), U3.12 (STNDBY), U4.1 (VCC), U5.1 (VDD), U6.22 (VCC), U7.2 (VCC), U7.12 (STNDBY)
+6V: J8.1, J14.1, U1.J2-19 (EXT_5V)
+12V: J13.1, U2.1 (VM), U3.1 (VM), U7.1 (VM)
/A1_A: J5.5, U1.J2-5 (IO34)
/A1_B: J5.6, U1.J2-6 (IO35)
/A1_IN_1: U3.11 (AIN1), U6.14 (P04)
/A1_IN_2: U3.10 (AIN2), U6.13 (P05)
/A1_OUT_1: J5.1, U3.4 (AO1)
/A1_OUT_2: J5.2, U3.5 (AO2)
/A1_PWM: U1.J3-12 (IO16), U3.9 (PWMA)
/A2_A: J6.5, U1.J2-3 (SENSOR_VP)
/A2_B: J6.6, U1.J2-4 (SENSOR_VN)
/A2_IN_1: U3.13 (BIN1), U6.12 (P06)
/A2_IN_2: U3.14 (BIN2), U6.11 (P07)
/A2_OUT_1: J6.1, U3.6 (BO1)
/A2_OUT_2: J6.2, U3.7 (BO2)
/A2_PWM: U1.J3-11 (IO17), U3.15 (PWMB)
/A3_A: J3.5, U1.J2-13 (IO12)
/A3_B: J3.6, U1.J2-15 (IO13)
/A3_IN_1: U6.1 (P10), U7.11 (AIN1)
/A3_IN_2: U6.2 (P11), U7.10 (AIN2)
/A3_OUT_1: J3.1, U7.4 (AO1)
/A3_OUT_2: J3.2, U7.5 (AO2)
/A3_PWM: U1.J3-9 (IO18), U7.9 (PWMA)
/A4_A: J4.5, U1.J2-12 (IO14)
/A4_B: J4.6, U1.J3-16 (IO15)
/A4_IN_1: U6.3 (P12), U7.13 (BIN1)
/A4_IN_2: U6.4 (P13), U7.14 (BIN2)
/A4_OUT_1: J4.1, U7.6 (BO1)
/A4_OUT_2: J4.2, U7.7 (BO2)
/A4_PWM: U1.J3-8 (IO19), U7.15 (PWMB)
/BMS_1: R1.2, R2.1, U5.7 (A0)
/BMS_2: R3.2, R4.1, U5.8 (A1)
/BMS_3: R5.2, R6.1, U5.9 (A2)
/BMS_IN_1: J7.1, R1.1
/BMS_IN_2: J7.2, R2.2, R3.1
/BMS_IN_3: J7.3, R4.2, R5.1
/BUTTON: SW3.2, U6.8 (P17)
/BUZZER: BZ1.1 (+), U1.J3-10 (IO5)
/CAM_RX: J8.4, U1.J2-9 (IO25)
/CAM_TX: J8.3, U1.J3-2 (IO23)
/LED: R7.1, U6.5 (P14)
/LIMIT_1: J9.2, U6.6 (P15)
/LIMIT_2: J10.2, U6.7 (P16)
/L_A: J1.5, U1.J2-10 (IO26)
/L_B: J1.6, U1.J2-11 (IO27)
/L_IN_1: U2.11 (AIN1), U6.18 (P00)
/L_IN_2: U2.10 (AIN2), U6.17 (P01)
/L_OUT_1: J1.1, U2.4 (AO1)
/L_OUT_2: J1.2, U2.5 (AO2)
/L_PWM: U1.J3-15 (IO2), U2.9 (PWMA)
/R_A: J2.5, U1.J2-7 (IO32)
/R_B: J2.6, U1.J2-8 (IO33)
/R_IN_1: U2.13 (BIN1), U6.16 (P02)
/R_IN_2: U2.14 (BIN2), U6.15 (P03)
/R_OUT_1: J2.1, U2.6 (BO1)
/R_OUT_2: J2.2, U2.7 (BO2)
/R_PWM: U1.J3-13 (IO4), U2.15 (PWMB)
/SCL: J15.4, U1.J3-3 (IO22), U4.3 (SCL), U5.3 (SCL), U6.24 (SCL)
/SDA: J15.5, U1.J3-6 (IO21), U4.4 (SDA), U5.4 (SDA), U6.23 (SDA)
GND: BZ1.2 (-), D1.1 (K), J1.3, J2.3, J3.3, J4.3, J5.3, J6.3, J7.4, J8.2, J13.2, J14.2, J15.2, R6.2, U1.J2-14 (GND1), U2.8 (GND), U2.16 (GND), U3.8 (GND), U3.16 (GND), U4.2 (GND), U4.7 (ADO), U5.2 (GND), U5.5 (ADDR), U6.21 (GND), U7.8 (GND), U7.16 (GND)
unnamed: D1.2 (A), R7.2

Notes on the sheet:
Sensors
Encoders
Power input
Wheels
Motor attachments
BMS
MCU
State Indication

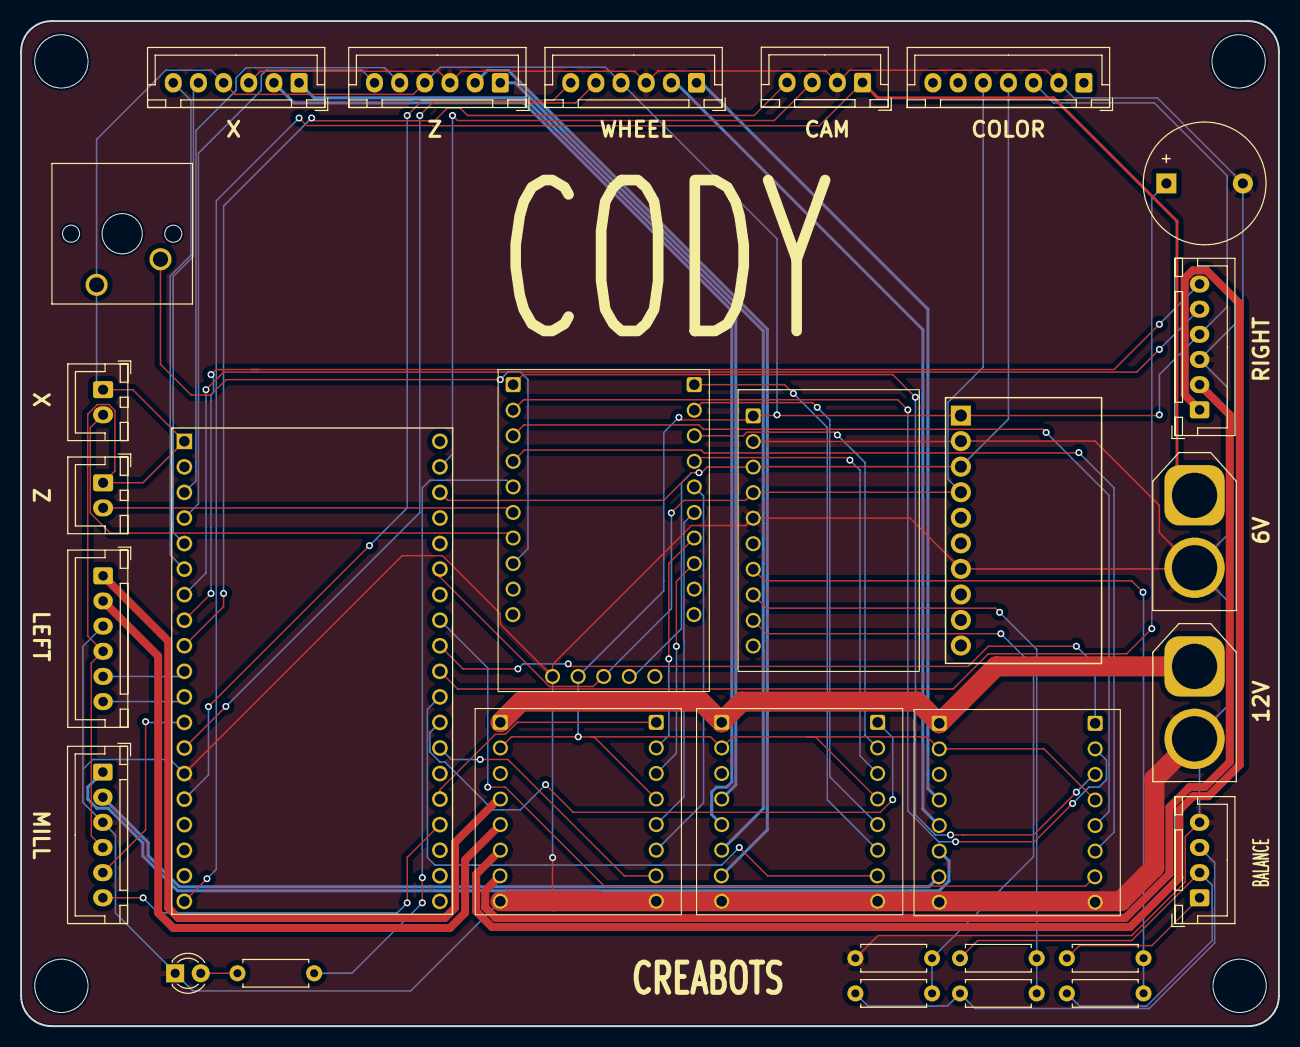
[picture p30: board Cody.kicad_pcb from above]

Board: 2 copper layers, 125.0 x 99.9 mm, 30 parts (0 on the bottom side), 62 nets.

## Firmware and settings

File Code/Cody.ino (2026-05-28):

// Global parameters
// #define SIMULATION
#define BAUD_RATE 115200

// Include dependencies
#include "Cody.h"
#include "BMS.h"
#include "Program.h"

#ifdef SIMULATION
  #include "SimulationDataProvider.h"
  #include "SimulationHardwareProvider.h"
  SimulationDataProvider dataProvider;
  SimulationHardwareProvider hardwareProvider;
#else
  #include "SensorDataProvider.h"
  #include "RobotHardwareProvider.h"
  SensorDataProvider dataProvider;
  RobotHardwareProvider hardwareProvider;
#endif

// Setup
void setup() {
  Serial.begin(BAUD_RATE);
  delay(3000);
  
  dataProvider.initialize();
  hardwareProvider.initialize();
  Cody::initialize(dataProvider, hardwareProvider);
  // BMS::initialize();

  delay(5000);

  // waitForButton();
  // Program::go();
}

void waitForButton() {
  SensorData sensorData;

  while (!sensorData.button) {
    sensorData = dataProvider.getData();
    delay(10);
  }
}

void loop() {

  GPIO::digitalWrite(15, LOW);
  Serial.println(GPIO::digitalRead(15));
  delay(100);

}

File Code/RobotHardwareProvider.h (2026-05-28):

#pragma once
#include "IHardwareProvider.h"
#include "GPIO.h"
#include "Cody.h"
#include <Arduino.h>
#include <Wire.h>

// PWM
#define L_PWM 2
#define R_PWM 4
#define A1_PWM 16 // X
#define A2_PWM 17 // Z
#define A3_PWM 18 // Wheels
#define A4_PWM 19 // Mill

// Direction
#define L_IN_1 0
#define L_IN_2 1
#define R_IN_1 2
#define R_IN_2 3
#define A1_IN_1 4
#define A1_IN_2 5
#define A2_IN_1 6
#define A2_IN_2 7
#define A3_IN_1 8
#define A3_IN_2 9
#define A4_IN_1 10
#define A4_IN_2 11

// State indication
#define LED 12
#define BUZZER 5

// PWM to PPM
#define WHEELS_MAX_PPM 36240

class RobotHardwareProvider : public IHardwareProvider {
  public:
    void initialize() override {
      pinMode(L_PWM, OUTPUT);
      pinMode(R_PWM, OUTPUT);
      pinMode(A1_PWM, OUTPUT);
      pinMode(A2_PWM, OUTPUT);
      pinMode(A3_PWM, OUTPUT);
      pinMode(A4_PWM, OUTPUT);
      pinMode(BUZZER, OUTPUT);
    }

    void move(NavigationData navigationData) override {
      //navigationData.leftMotor.pwm *= 0.9;
      moveMotor(navigationData.leftMotor, L_IN_1, L_IN_2, L_PWM);
      moveMotor(navigationData.rightMotor, R_IN_1, R_IN_2, R_PWM);
    }

    void moveToolhead(ToolheadData toolheadData) override {
      moveMotor(toolheadData.xAxisMotor, A1_IN_1, A1_IN_2, A1_PWM);
      moveMotor(toolheadData.zAxisMotor, A2_IN_1, A2_IN_2, A2_PWM);
    }

    void moveWheels(WheelsData wheelsData) override {
      moveMotor(wheelsData.wheelsMotor, A3_IN_1, A3_IN_2, A3_PWM);
    }

    void moveMill(MillData millData) override {
      moveMotor(millData.millMotor, A4_IN_1, A4_IN_2, A4_PWM);
    }

    void writeLed(uint8_t value) override {
      GPIO::digitalWrite(LED, value);
    }

    void toneBuzzer(unsigned int frequency, unsigned long duration = 0) override {
      if (duration == 0) tone(BUZZER, frequency);
      else tone(BUZZER, frequency, duration);
    }

    void noToneBuzzer() override {
      noTone(BUZZER);
    }

  private:
    void moveMotor(MotorData motorData, unsigned int in1, unsigned int in2, unsigned int pwm) {
      if (motorData.forwards) {
        GPIO::digitalWrite(in1, HIGH);
        GPIO::digitalWrite(in2, LOW);
      } else {
        GPIO::digitalWrite(in1, LOW);
        GPIO::digitalWrite(in2, HIGH);
      }

      analogWrite(pwm, motorData.pwm);
    }
};

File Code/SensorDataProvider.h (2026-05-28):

#pragma once
#include "IDataProvider.h"
#include "GPIO.h"
#include "TCS34725.h"
#include <Arduino.h>
#include <Wire.h>
#include <ESP32Encoder.h>
#include <FastIMU.h>
#include <ADS1115_WE.h>
#include <Wire.h>

#define IMU_ADDRESS 0x68
#define ADS_ADDRESS 0x48
#define G 9.807
#define DEG2RAD 0.01745329251f

// Encoders
#define L_A 26
#define L_B 27
#define R_A 32
#define R_B 33
#define A1_A 34
#define A1_B 35
#define A2_A 36
#define A2_B 39
#define A3_A 12
#define A3_B 13
#define A4_A 14
#define A4_B 15

// Switches
#define LIMIT_1 13
#define LIMIT_2 14
#define BUTTON 15

// Sensors
ADS1115_WE ADS = ADS1115_WE(ADS_ADDRESS);
TCS34725 TCS;

class SensorDataProvider : public IDataProvider {
  public:
    void initialize() override {
      // Initialize IMU
      Wire.begin();
      Wire.setClock(400000);

      IMU.setIMUGeometry(7);
      int error = IMU.init({ 0 }, IMU_ADDRESS);

      if (error != 0) {
        Serial.print("Error initializing IMU: ");
        Serial.println(error);
      }

      // Initialize ADS1115
      Wire.begin();

      while (!ADS.init()) {
        Serial.println("Initializing ADS");
        delay(1);
      }

      ADS.setVoltageRange_mV(ADS1115_RANGE_6144);
      ADS.setMeasureMode(ADS1115_CONTINUOUS);

      // Initialize TCS34725
      /*
      while (!TCS.attach(Wire)) {
        Serial.println("Initializing TCS");
        delay(1);
      }

      TCS.integrationTime(1000.0 / HZ);
      TCS.gain(TCS34725::Gain::X01);*/

      // Initialize PCF8575
      GPIO::initialize();
      
      // Initialize encoders
      leftEncoder.attachHalfQuad(L_A, L_B);
      leftEncoder.setCount(0);
      rightEncoder.attachHalfQuad(R_A, R_B);
      rightEncoder.setCount(0);
      xEncoder.attachHalfQuad(A1_A, A1_B);
      xEncoder.setCount(0);
      zEncoder.attachHalfQuad(A2_A, A2_B);
      zEncoder.setCount(0);
      wheelsEncoder.attachHalfQuad(A3_A, A3_B);
      wheelsEncoder.setCount(0);
      millEncoder.attachHalfQuad(A4_A, A4_B);
      millEncoder.setCount(0);
    }

    SensorData getData() override {
      SensorData data;

      // Get IMU data
      /*IMU.update();
      data.acceleration = readAccelerometer();
      data.gyroscope = readGyroscope();
      data.magnetometer = readMagnetometer();*/

      // Get wheel pulses
      data.leftPulses = leftEncoder.getCount();
      data.rightPulses = -rightEncoder.getCount();
      data.xAxisPulses = xEncoder.getCount();
      data.zAxisPulses = zEncoder.getCount();
      data.wheelsPulses = wheelsEncoder.getCount();
      data.millPulses = millEncoder.getCount();

      // Get color sensor
      /*if (TCS.available()) {
          TCS34725::Color color = TCS.color();
          data.colorData = ColorData(color.r, color.g, color.b);
      }*/

      // Get BMS
      data.bms1 = readVoltage(ADS1115_COMP_0_GND);
      data.bms2 = readVoltage(ADS1115_COMP_1_GND);
      data.bms3 = readVoltage(ADS1115_COMP_3_GND);

      // Get switches
      data.xLimit = GPIO::digitalRead(LIMIT_2) == 1;
      data.zLimit = GPIO::digitalRead(LIMIT_1) == 1;
      data.button = GPIO::digitalRead(BUTTON) == 1;

      return data;
    }

  private:
    // Encoders
    ESP32Encoder leftEncoder;
    ESP32Encoder rightEncoder;
    ESP32Encoder xEncoder;
    ESP32Encoder zEncoder;
    ESP32Encoder wheelsEncoder;
    ESP32Encoder millEncoder;

    // Orientation
    MPU9250 IMU;
    AccelData accelData;
    GyroData gyroData;
    MagData magData;

    Vector3 readAccelerometer() {
      Vector3 acceleration;
      IMU.getAccel(&accelData);
      acceleration.x = accelData.accelX * G;
      acceleration.y = accelData.accelY * G;
      acceleration.z = accelData.accelZ * G;

      return acceleration;
    }

    Vector3 readGyroscope() {
      Vector3 gyroscope;
      IMU.getGyro(&gyroData);
      gyroscope.x = gyroData.gyroX * DEG2RAD;
      gyroscope.y = gyroData.gyroY * DEG2RAD;
      gyroscope.z = gyroData.gyroZ * DEG2RAD;

      return gyroscope;
    }

    Vector3 readMagnetometer() {
      Vector3 magnetometer;
      IMU.getMag(&magData);
      magnetometer.x = magData.magX;
      magnetometer.y = magData.magY;
      magnetometer.z = magData.magZ;

      return magnetometer;
    }

    double readVoltage(ADS1115_MUX channel) {
      ADS.setCompareChannels(channel);
      return ADS.getResult_V();
    }
};

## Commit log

2026-04-08 Switch computers
2026-05-01 Added wheels and robot hardware
    [Main.3mf, Main.sync-conflict-20260428-161026-ZBDHWGP.3mf, Prototypes.3mf]
2026-05-07 Added sensors and state indication
    [Cody-B_Cu.sync-conflict-20260325-102323-DWRB73V.gbr, Cody-B_Mask.sync-conflict-20260325-102322-DWRB73V.gbr, Cody-B_Silkscreen.sync-conflict-20260325-102323-DWR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]
2026-05-07 Added toolhead homing
    [Main.3mf]
2026-05-15 Added mill
    [Main.3mf]
2026-05-22 Integrated testing
    [Main.3mf]
2026-05-28 Working GPIO expander
    [Main.3mf]
